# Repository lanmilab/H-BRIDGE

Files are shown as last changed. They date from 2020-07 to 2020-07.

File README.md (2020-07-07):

# H-BRIDGE
High Power High Speed MOSFET H-Bridge

Image description
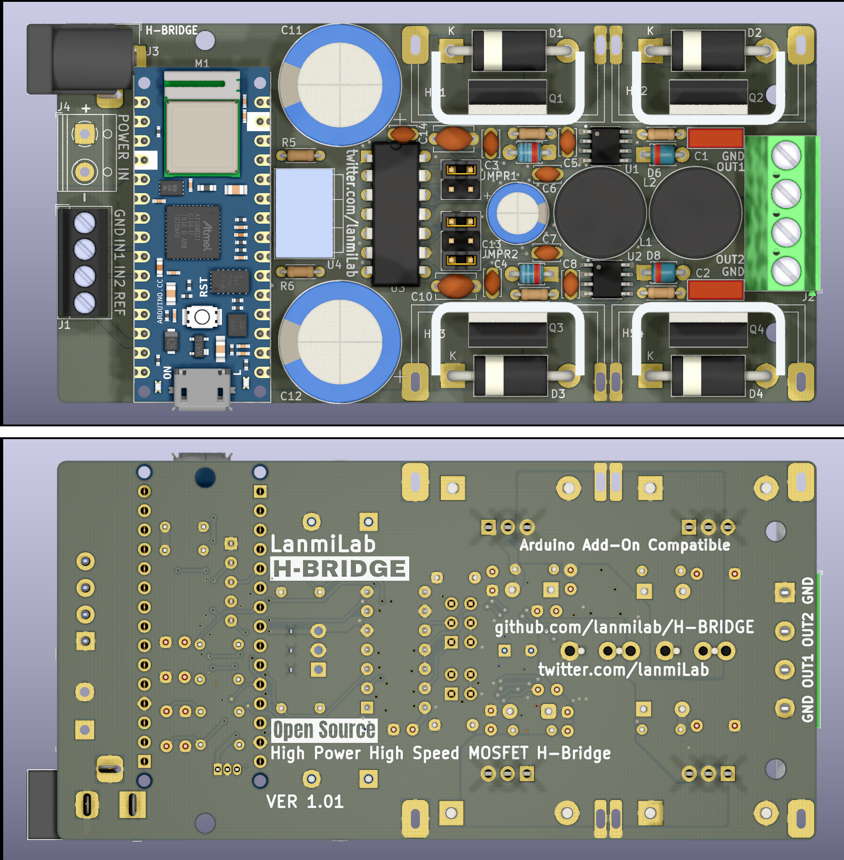
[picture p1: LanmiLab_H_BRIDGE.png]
Image description


2 X Half-Bridge or Full H-Bridge.
Digital TTL/CMOS or PWM inputs.
Features Add-On headers Compatible to Arduino Nano.

Typical Applications:
  - Power Stage in Class-D Power Amplifiers
  Image description
  - DC Motor Drivers
  - DC/DC Switching power converters
  - LED Drivers

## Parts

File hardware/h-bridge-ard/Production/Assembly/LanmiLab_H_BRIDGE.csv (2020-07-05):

Reference | Quantity | Value | Footprint | Datasheet | Part Number | Alternative | Note
C10 C9 | 2 | 4.7uF | Capacitor_THT:C_Disc_D5.1mm_W3.2mm_P5.00mm | http://www.farnell.com/datasheets/2728346.pdf | RDEC72A475MWK1H03B
C12 C11 | 2 | 1000uF/63V | Capacitor_THT:CP_Radial_D16.0mm_P7.50mm | https://www.mouser.com/datasheet/2/315/ABA0000C1218-1131230.pdf | EEUFC1J102U
C13 | 1 | 100uF/63V | Capacitor_THT:CP_Radial_D8.0mm_P3.50mm | https://www.mouser.com/datasheet/2/315/ABA0000C1218-1131230.pdf | ECA-1JM101
C14 C4 C8 C7 C3 C6 C5 | 7 | 100nF/50V | Capacitor_THT:C_Disc_D3.4mm_W2.1mm_P2.50mm | http://www.farnell.com/datasheets/2045792.pdf | K104K15X7RF53L2
C15 C16 C17 C18 | 4 | 1.8nF | Capacitor_THT:C_Rect_L4.0mm_W2.5mm_P2.50mm | http://www.farnell.com/datasheets/2739049.pdf | C320C182J1G5TA
C2 C1 | 2 | 220nF | Capacitor_THT:C_Rect_L7.2mm_W2.5mm_P5.00mm_FKS2_FKP2_MKS2_MKP2 | http://www.farnell.com/datasheets/2752854.pdf | R82DC3220Z360J
D4 D3 D2 D1 | 4 | MBR360 | Diode_THT:D_DO-201AD_P15.24mm_Horizontal | http://www.onsemi.com/pub_link/Collateral/MBR340-D.PDF | MBR360G
D8 D7 D6 D5 | 4 | D_Schottky_Small | Diode_THT:D_T-1_P5.08mm_Horizontal | https://www.diodes.com/assets/Datasheets/ds11009.pdf | SD103B-F
H1 H2 H3 H4 | 4 | MountingHole_Pad | MountingHole:MountingHole_2.1mm | ~ |  |  | M2.5 Bolt
HS1 HS2 HS3 HS4 | 4 | Heatsink_Pad | _Heatsink:Heatsink_AAVID_6021BG_25.4x12.7mm__Solderable | https://www.boydcorp.com/aavid-datasheets/Board-Level-Cooling-Channel-6021.pdf | 6021BG | 590102B03600G
J1 | 1 | Screw_Terminal_01x04 | TerminalBlock_4Ucon:TerminalBlock_4Ucon_1x04_P3.50mm_Horizontal | http://www.farnell.com/datasheets/1838842.pdf | 31059104
J2 | 1 | Screw_Terminal_01x04 | TerminalBlock_Phoenix:TerminalBlock_Phoenix_MKDS-1,5-4-5.08_1x04_P5.08mm_Horizontal | http://www.farnell.com/datasheets/2363060.pdf | MKDS 1,5/ 4
J3 | 1 | Barrel_Jack_Switch | Barrel_Jack:BarrelJack_Horizontal | https://www.we-online.de/katalog/datasheet/6941xx301002.pdf | 6.94106E+11
J4 | 1 | Screw_Terminal_01x02 | TerminalBlock_RND:TerminalBlock_RND_205-00012_1x02_P5.00mm_Horizontal | http://www.farnell.com/datasheets/2336346.pdf | 31320102
JMPR1 | 1 | Conn_02x02_Odd_Even | Connector_PinHeader_2.54mm:PinHeader_2x02_P2.54mm_Vertical | ~ | 10-89-7041
JMPR2 | 1 | Conn_02x03_Odd_Even | Connector_PinHeader_2.54mm:PinHeader_2x03_P2.54mm_Vertical | ~ | 10-89-7061
JP2 JP1 | 2 | SolderJumper_3_Bridged12 | Jumper:SolderJumper-3_P1.3mm_Bridged12_RoundedPad1.0x1.5mm_NumberLabels | ~ |  |  | Not Populated, Configuration Jumper
JP3 | 1 | Jumper_NO_Small | Jumper:SolderJumper-2_P1.3mm_Open_RoundedPad1.0x1.5mm | ~ |  |  | Not Populated, Configuration Jumper
JPC2 JPC3 JPC1 | 3 | JumperCap | _Jumper:ShortingJumperCap-2_P2.54mm | http://www.farnell.com/datasheets/39272.pdf?_ga=2.94235675.720265721.1581510996-797642152.1567873553 | 2-382811-0
L2 L1 | 2 | 4.7uH | Inductor_THT:L_Radial_D12.0mm_P5.00mm_Neosid_SD12k_style2 | http://www.farnell.com/datasheets/1951882.pdf?_ga=2.928049.120407668.1580559680-797642152.1567873553 | 744750340047
M1 | 1 | Arduino_Nano_v3.x_plug | Module:Arduino_Nano_33_IoT_3D_NoPads | https://www.arduino.cc/en/uploads/Main/ArduinoNanoManual23.pdf |  |  | Add-on Board
P2 P1 | 2 | Conn_01x15 | Connector_PinSocket_2.54mm:PinSocket_1x15_P2.54mm_Vertical | https://media.digikey.com/pdf/Data%20Sheets/Sullins%20PDFs/Female_Headers.100_DS.pdf | PPPC151LFBN-RC
Q4 Q3 Q2 Q1 | 4 | NMOSFET | Package_TO_SOT_THT:TO-220-3_Vertical | https://www.st.com/resource/en/datasheet/stp25n10f7.pdf | STP25N10F7
R4 R3 R2 R1 | 4 | 4R7 | Resistor_THT:R_Axial_DIN0204_L3.6mm_D1.6mm_P5.08mm_Horizontal | http://www.farnell.com/datasheets/1723854.pdf | CFR16J4R7
R5 R6 R9 R10 R11 R12 | 6 | 47K | Resistor_THT:R_Axial_DIN0204_L3.6mm_D1.6mm_P5.08mm_Horizontal | http://www.farnell.com/datasheets/1723854.pdf | LR0204F47K
R7 R8 | 2 | 4K7 | Resistor_THT:R_Axial_DIN0204_L3.6mm_D1.6mm_P5.08mm_Horizontal | http://www.farnell.com/datasheets/1723854.pdf | CFR16J4K7
RN1 | 1 | 3K3 | Resistor_THT:R_Array_SIP5 | http://www.farnell.com/datasheets/682196.pdf | 4605X-101-332LF
U2 U1 | 2 | HIP2101_SOIC | Package_SO:SOIC-8_3.9x4.9mm_P1.27mm | http://www.intersil.com/content/dam/Intersil/documents/hip2/hip2101.pdf | HIP2101IBZT | UCC27211D
U3 | 1 | 6 x Hex Inverter | Package_DIP:DIP-14_W7.62mm | http://www.ti.com/lit/ds/symlink/sn74s04.pdf | SN74S04N
U4 | 1 | DC/DC 9V/500mA | TO:TO-220-3_SRH05S09 | https://www.xppower.com/portals/0/pdfs/SF_SRH05.pdf | SRH05S09
U5 | 1 | DC/DC 5V/100mA | Package_TO_SOT_THT:TO-92_Inline | http://www.fairchildsemi.com/ds/LM/LM78L05A.pdf | LM78L05ACZ/NOPB

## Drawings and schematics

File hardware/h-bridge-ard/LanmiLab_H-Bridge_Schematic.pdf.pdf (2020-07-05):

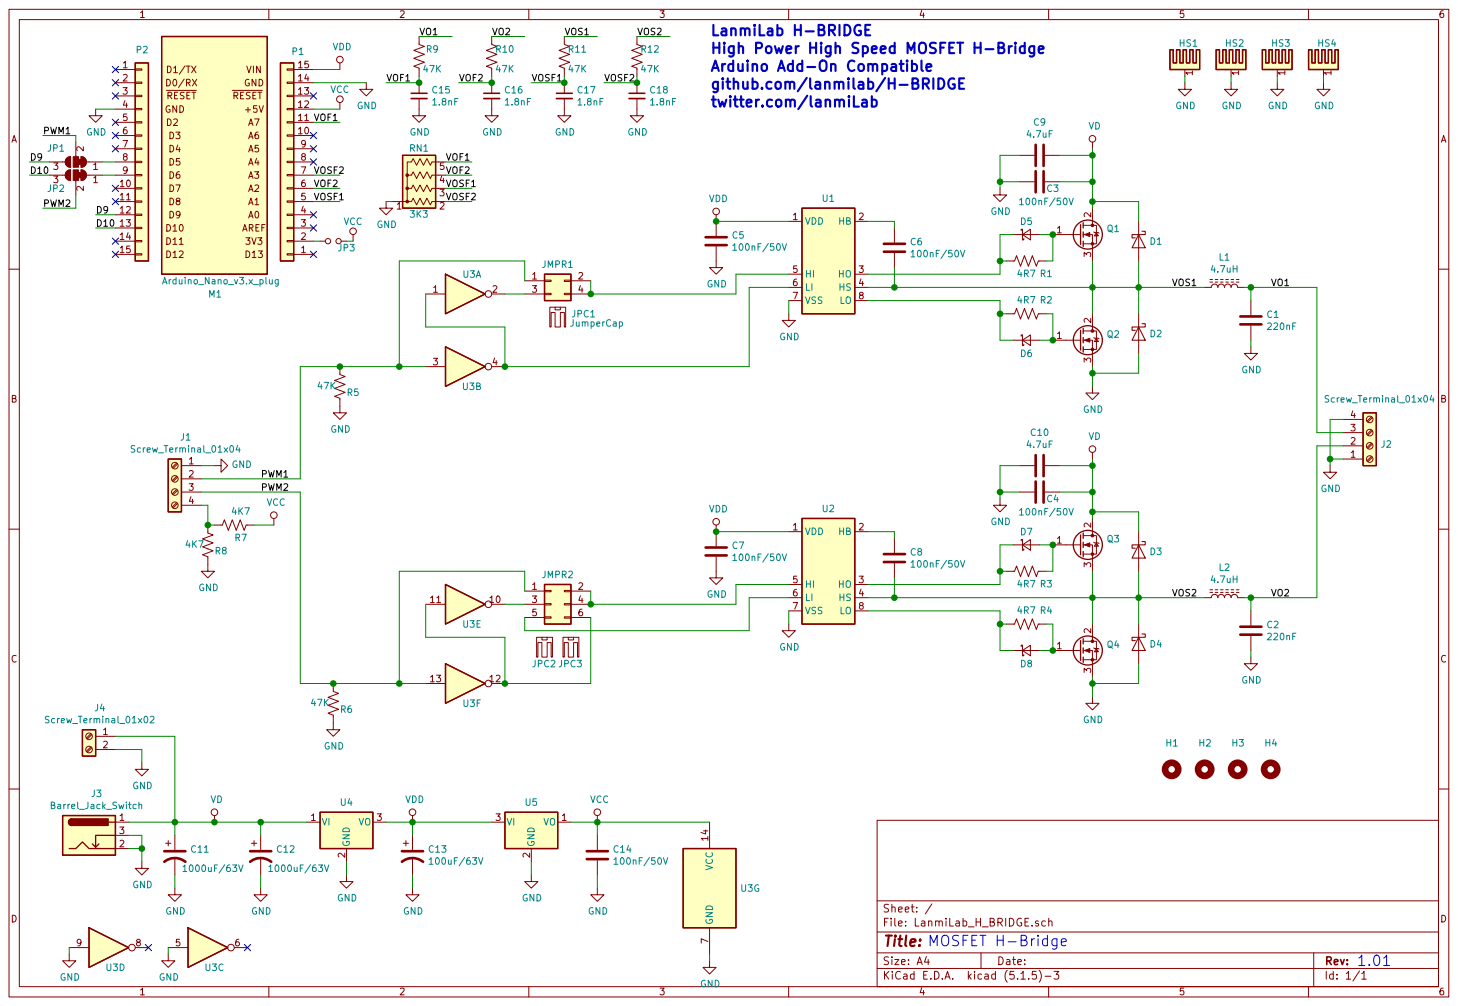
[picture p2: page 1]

LanmiLab H-BRIDGE
High Power High Speed MOSFET H-Bridge
Arduino Add-On Compatible
github.com/lanmilab/H-BRIDGE
twitter.com/lanmiLab

1 HS1 GND GND GND GND

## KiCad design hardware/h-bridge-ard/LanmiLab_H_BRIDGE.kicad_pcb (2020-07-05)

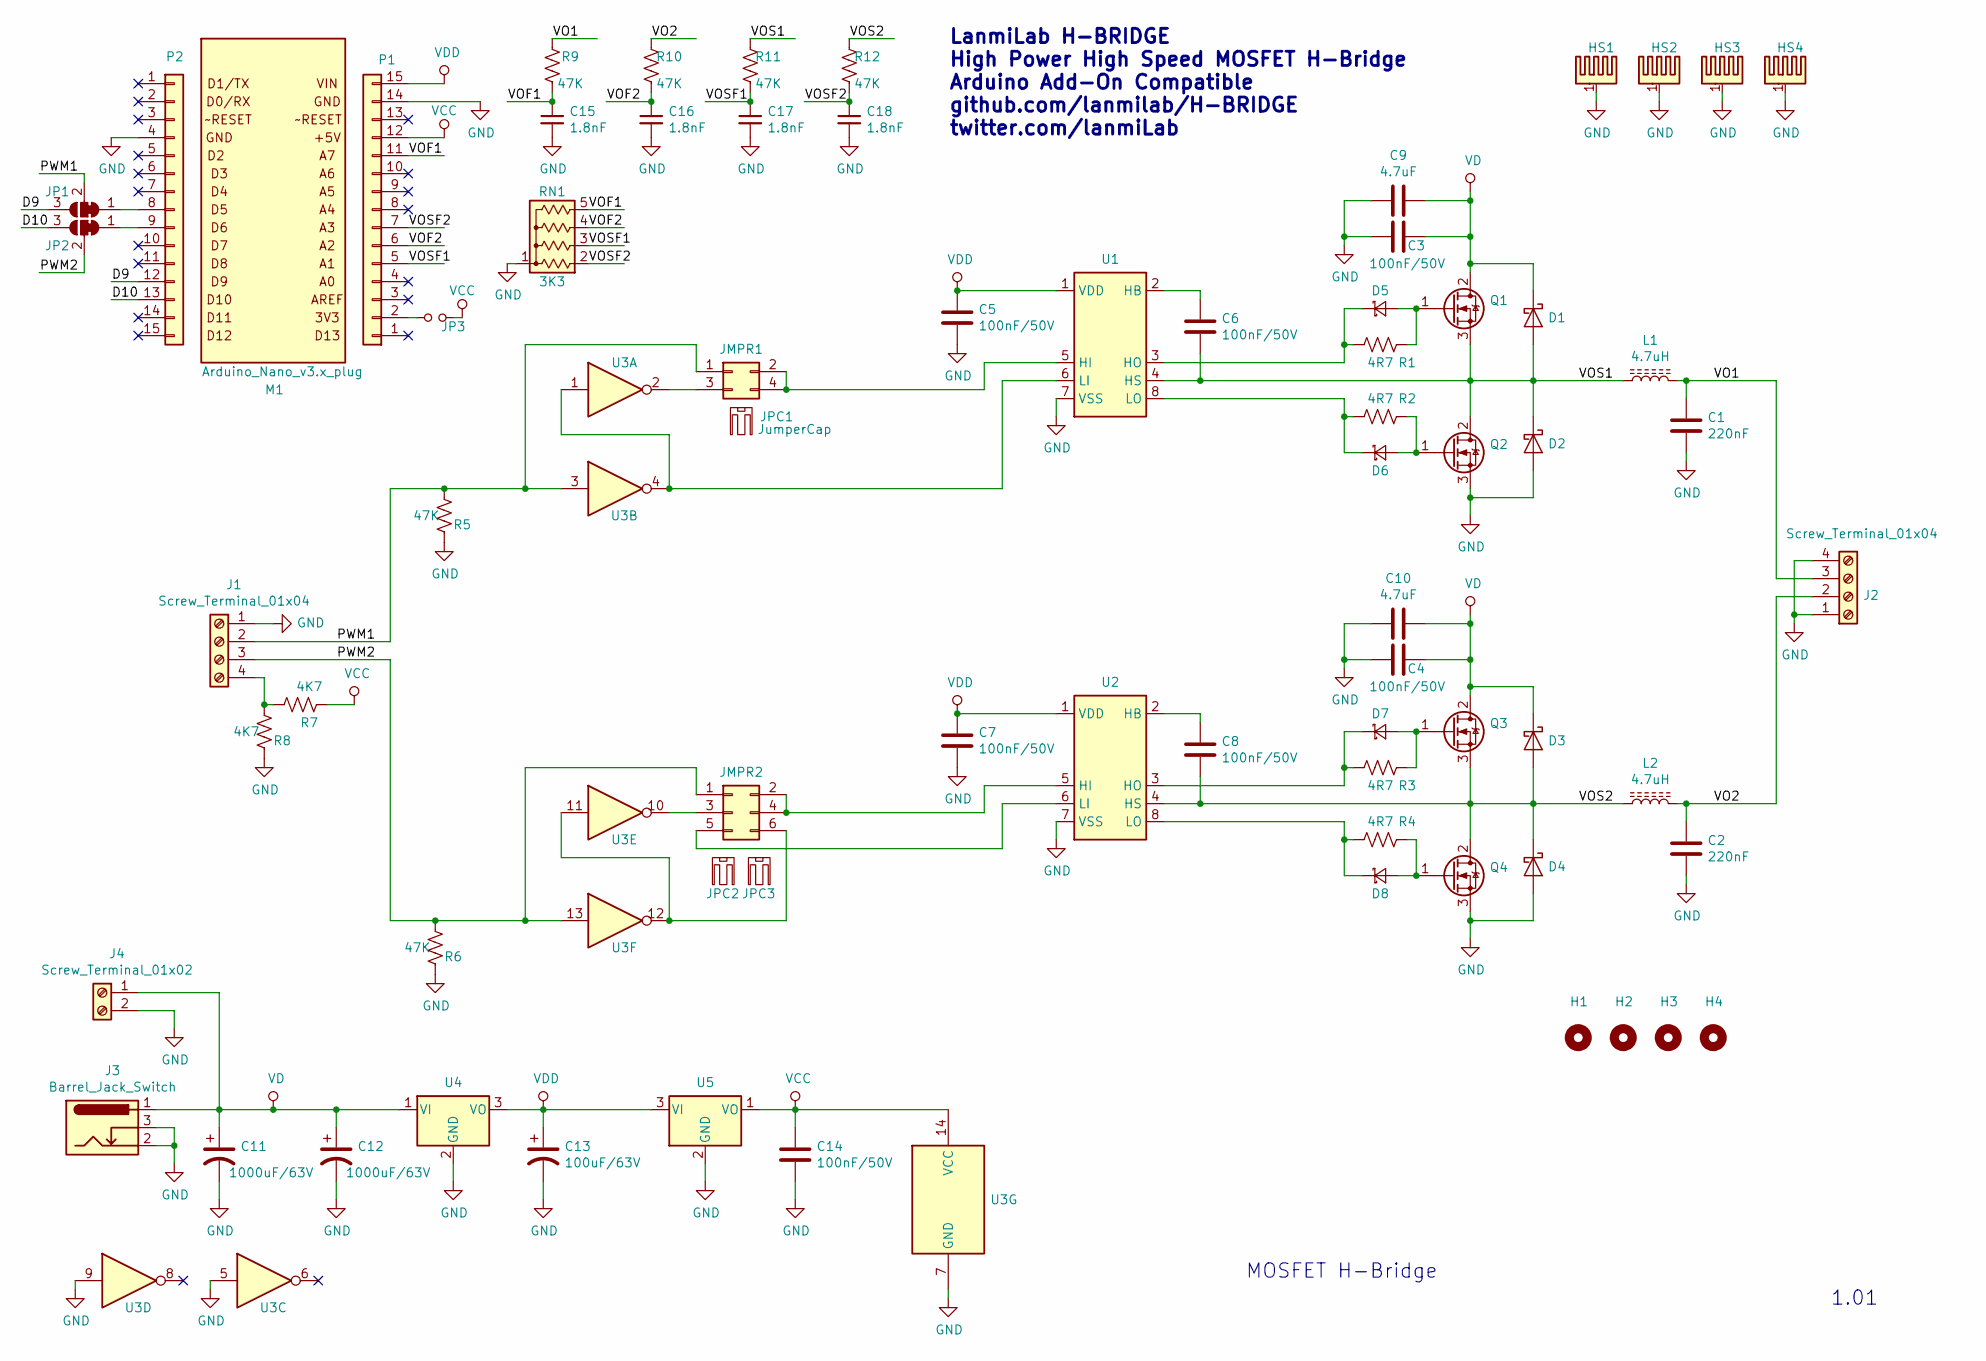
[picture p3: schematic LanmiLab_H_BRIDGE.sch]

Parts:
C1, C2: 220nF; C_Rect_L7.2mm_W2.5mm_P5.00mm_FKS2_FKP2_MKS2_MKP2; Part Number R82DC3220Z360J
C3, C4, C5, C6, C7, C8, C14: 100nF/50V; C_Disc_D3.4mm_W2.1mm_P2.50mm; Part Number K104K15X7RF53L2
C9, C10: 4.7uF; C_Disc_D5.1mm_W3.2mm_P5.00mm; Part Number RDEC72A475MWK1H03B
C11, C12: 1000uF/63V; CP_Radial_D16.0mm_P7.50mm; Part Number EEUFC1J102U
C13: 100uF/63V; CP_Radial_D8.0mm_P3.50mm; Part Number ECA-1JM101
C15, C16, C17, C18: 1.8nF; C_Rect_L4.0mm_W2.5mm_P2.50mm; Part Number C320C182J1G5TA
D1, D2, D3, D4: MBR360; D_DO-201AD_P15.24mm_Horizontal; Part Number MBR360G
D5, D6, D7, D8: D_Schottky_Small; D_T-1_P5.08mm_Horizontal; Part Number SD103B-F
H1, H2, H3, H4: MountingHole_Pad; MountingHole_2.1mm
HS1, HS2, HS3, HS4: Heatsink_Pad; Heatsink_AAVID_6021BG_25.4x12.7mm__Solderable; Part Number 6021BG
J1: Screw_Terminal_01x04; TerminalBlock_4Ucon_1x04_P3.50mm_Horizontal; Part Number 31059104
J2: Screw_Terminal_01x04; TerminalBlock_Phoenix_MKDS-1,5-4-5.08_1x04_P5.08mm_Horizont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; Part Number MKDS 1,5/ 4
J3: Barrel_Jack_Switch; BarrelJack_Horizontal; Part Number 694106301002
J4: Screw_Terminal_01x02; TerminalBlock_RND_205-00012_1x02_P5.00mm_Horizontal; Part Number 31320102
JMPR1: Conn_02x02_Odd_Even; PinHeader_2x02_P2.54mm_Vertical; Part Number 10-89-7041
JMPR2: Conn_02x03_Odd_Even; PinHeader_2x03_P2.54mm_Vertical; Part Number 10-89-7061
JP1, JP2: SolderJumper_3_Bridged12; SolderJumper-3_P1.3mm_Bridged12_RoundedPad1.0x1.5mm_NumberL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
JP3: Jumper_NO_Small; SolderJumper-2_P1.3mm_Open_RoundedPad1.0x1.5mm
JPC1, JPC2, JPC3: JumperCap; ShortingJumperCap-2_P2.54mm; Part Number 2-382811-0
L1, L2: 4.7uH; L_Radial_D12.0mm_P5.00mm_Neosid_SD12k_style2; Part Number 744750530047
M1: Arduino_Nano_v3.x_plug; Arduino_Nano_33_IoT_3D_NoPads
P1, P2: Conn_01x15; PinSocket_1x15_P2.54mm_Vertical; Part Number PPPC151LFBN-RC
Q1, Q2, Q3, Q4: NMOSFET; TO-220-3_Vertical; Part Number STP25N10F7
R1, R2, R3, R4: 4R7; R_Axial_DIN0204_L3.6mm_D1.6mm_P5.08mm_Horizontal; Part Number CFR16J4R7
R5, R6, R9, R10, R11, R12: 47K; R_Axial_DIN0204_L3.6mm_D1.6mm_P5.08mm_Horizontal; Part Number LR0204F47K
R7, R8: 4K7; R_Axial_DIN0204_L3.6mm_D1.6mm_P5.08mm_Horizontal; Part Number CFR16J4K7
RN1: 3K3; R_Array_SIP5; Part Number 4605X-101-332LF
U1, U2: HIP2101_SOIC; SOIC-8_3.9x4.9mm_P1.27mm; Part Number HIP2101IBZT
U3: 6 x Hex Inverter; DIP-14_W7.62mm; Part Number SN74S04N
U4: DC/DC 9V/500mA; TO-220-3_SRH05S09; Part Number SRH05S09
U5: DC/DC 5V/100mA; TO-92_Inline; Part Number LM78L05ACZ/NOPB

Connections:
/D9: JP1.3 (B), P2.12
/D10: JP2.3 (B), P2.13
/PWM1: J1.2, JMPR1.1, JP1.2 (C), R5.2, U3.3
/PWM2: J1.3, JMPR2.1, JP2.2 (C), R6.2, U3.13
/VO1: C1.1, J2.3, L1.2, R9.2
/VO2: C2.1, J2.2, L2.2, R10.2
/VOF1: C15.1, P1.11, R9.1, RN1.5 (R4)
/VOF2: C16.1, P1.6, R10.1, RN1.4 (R3)
/VOS1: C6.2, D1.2 (A), D2.1 (K), L1.1, Q1.3 (S), Q2.2 (D), R11.2, U1.4 (HS)
/VOS2: C8.2, D3.2 (A), D4.1 (K), L2.1, Q3.3 (S), Q4.2 (D), R12.2, U2.4 (HS)
/VOSF1: C17.1, P1.5, R11.1, RN1.3 (R2)
/VOSF2: C18.1, P1.7, R12.1, RN1.2 (R1)
GND: C1.2, C2.2, C3.2, C4.2, C5.2, C7.2, C9.2, C10.2, C11.2, C12.2, C13.2, C14.2, C15.2, C16.2, C17.2, C18.2, D2.2 (A), D4.2 (A), HS1.1, HS2.1, HS3.1, HS4.1, J1.1, J2.1, J2.4, J3.2, J3.3, J4.2, P1.14, P2.4, Q2.3 (S), Q4.3 (S), R5.1, R6.1, R8.1, RN1.1 (common), U1.7 (VSS), U2.7 (VSS), U3.5, U3.7 (GND), U3.9, U4.2 (GND), U5.2 (GND)
unnamed: C6.1, U1.2 (HB)
unnamed: C8.1, U2.2 (HB)
unnamed: D5.1 (K), R1.1, U1.3 (HO)
unnamed: D5.2 (A), Q1.1 (G), R1.2
unnamed: D6.1 (K), R2.1, U1.8 (LO)
unnamed: D6.2 (A), Q2.1 (G), R2.2
unnamed: D7.1 (K), R3.1, U2.3 (HO)
unnamed: D7.2 (A), Q3.1 (G), R3.2
unnamed: D8.1 (K), R4.1, U2.8 (LO)
unnamed: D8.2 (A), Q4.1 (G), R4.2
unnamed: J1.4, R7.1, R8.2
unnamed: JMPR1.2, JMPR1.4, U1.5 (HI)
unnamed: JMPR1.3, U3.2
unnamed: JMPR2.2, JMPR2.4, U2.5 (HI)
unnamed: JMPR2.3, U3.10
unnamed: JMPR2.5, U2.6 (LI)
unnamed: JMPR2.6, U3.11, U3.12
unnamed: JP1.1 (A), P2.8
unnamed: JP2.1 (A), P2.9
unnamed: JP3.1, P1.2
unnamed: U1.6 (LI), U3.1, U3.4
VCC: C14.1, JP3.2, P1.12, R7.2, U3.14 (VCC), U5.1 (VO)
VD: C3.1, C4.1, C9.1, C10.1, C11.1, C12.1, D1.1 (K), D3.1 (K), J3.1, J4.1, Q1.2 (D), Q3.2 (D), U4.1 (VI)
VDD: C5.1, C7.1, C13.1, P1.15, U1.1 (VDD), U2.1 (VDD), U4.3 (VO), U5.3 (VI)

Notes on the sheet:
MOSFET H-Bridge
LanmiLab H-BRIDGE High Power High Speed MOSFET H-Bridge Arduino Add-On Compatible github.com/lanmilab/H-BRIDGE twitter.com/lanmiLab
1.01

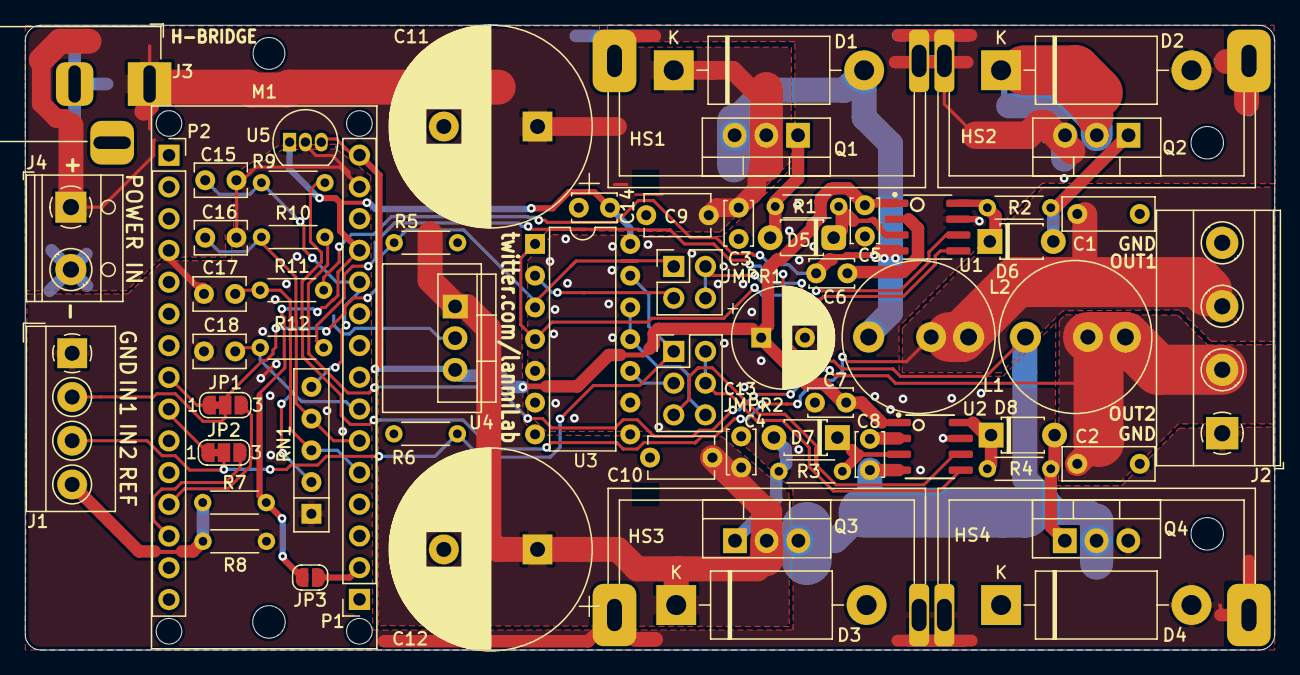
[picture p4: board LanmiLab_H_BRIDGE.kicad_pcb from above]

Board: 2 copper layers, 100.0 x 50.0 mm, 73 parts (0 on the bottom side), 37 nets.

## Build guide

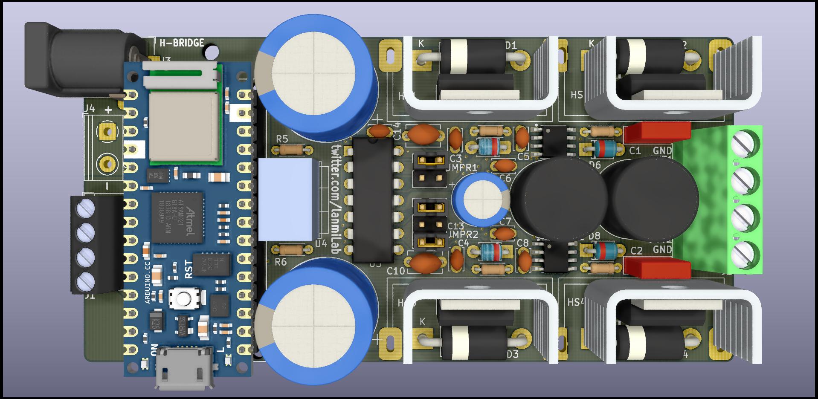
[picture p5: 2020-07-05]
hardware/h-bridge-ard/Production/Assembly/LanmiLab_H-Bridge_Realistic_Top.jpg

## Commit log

2020-02-12 Finished PCB Design
    [UHELIOS_MOSFET_BRIDGE.kicad_pcb, UHELIOS_MOSFET_BRIDGE.sch]
2020-02-12 PCB Fabrication gerbers added
2020-02-12 Finished V1.0 Design Files
    [UHELIOS_MOSFET_BRIDGE.kicad_pcb, UHELIOS_MOSFET_BRIDGE.sch]
2020-07-05 Silkscreen update
    [LanmiLab_H_BRIDGE.kicad_pcb, LanmiLab_H_BRIDGE.sch]
2020-07-05 V1.01 release
    [LanmiLab_H_BRIDGE.csv]
2020-07-05 Inductor part number change
    [LanmiLab_H_BRIDGE.sch]
